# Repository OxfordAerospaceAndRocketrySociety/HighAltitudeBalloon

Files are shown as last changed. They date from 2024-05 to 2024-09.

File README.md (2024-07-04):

# HighAltitudeBalloon
A raspberry pi pico based GPS tracker and reciever for high altitude ballooning.

Please read [Setup.md](https://github.com/OxfordAerospaceAndRocketrySociety/HighAltitudeBalloon/blob/main/Setup.md) for instructions on installing the dependencies.

Please also have a look at [TODO.md](https://github.com/OxfordAerospaceAndRocketrySociety/HighAltitudeBalloon/blob/main/TODO.md) for infomation about what is yet to be done!

To build your own please see [Wiring.md](https://github.com/OxfordAerospaceAndRocketrySociety/HighAltitudeBalloon/blob/main/Wiring.md), it has a table of all of the connections nececary.

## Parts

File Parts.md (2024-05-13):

### GPS Module x1  - £23.99:
https://store.uputronics.com/index.php?route=product/product&path=60_64&product_id=72
### LORA Transciever x5 - £9.50:
https://store.uputronics.com/index.php?route=product/product&path=61&product_id=69
### Pi Pico (Reciever MCU) x3 - £4.42:
https://uk.rs-online.com/web/p/raspberry-pi/2122162?gb=s
### Pi SD Card x1 - £7.08:
https://uk.rs-online.com/web/p/sd-cards/1958347?gb=s
### Micro usb cable (5 pack) - £6.99:
https://www.amazon.co.uk/PEAKLIFT-Charging-Charger-Compatible-Motorola/dp/B098JMKVDL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
### AA Power Bank x1 - £5.99:
https://www.amazon.co.uk/Mercury-Emergency-USB-Power-Bank/dp/B0168K5FTQ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
### Lithium Batteries (4 pack) x1 - £7.99:
https://www.amazon.co.uk/Energizer-Ultimate-Lithium-Batteries-Pack/dp/B000IWW1G6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

We also need some single core wire for antennae, and connecting the components.

## Total: £103.96

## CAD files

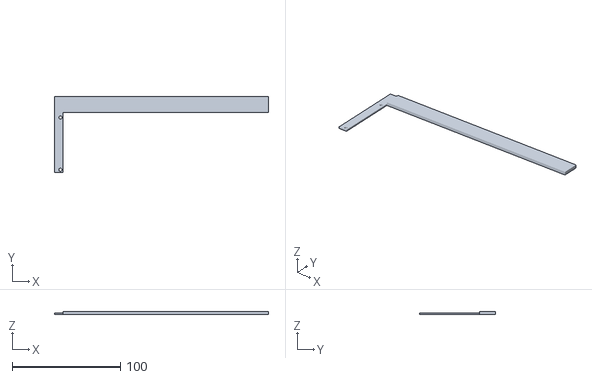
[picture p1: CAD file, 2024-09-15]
3D Printed Parts/RightSide.stl
198.0 x 70.3 x 3.00

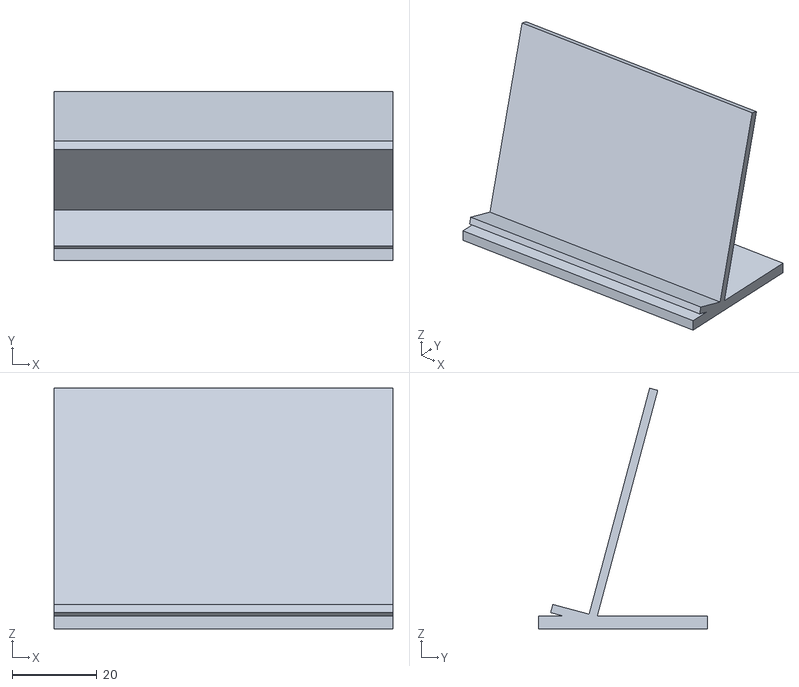
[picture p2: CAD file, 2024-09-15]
3D Printed Parts/Stand.stl
80.0 x 40.0 x 56.8

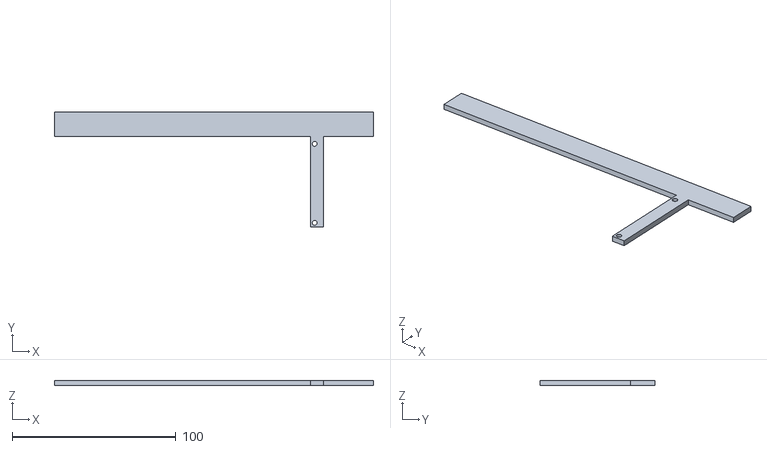
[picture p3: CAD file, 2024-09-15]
3D Printed Parts/LeftSide.stl
195.0 x 70.3 x 3.00

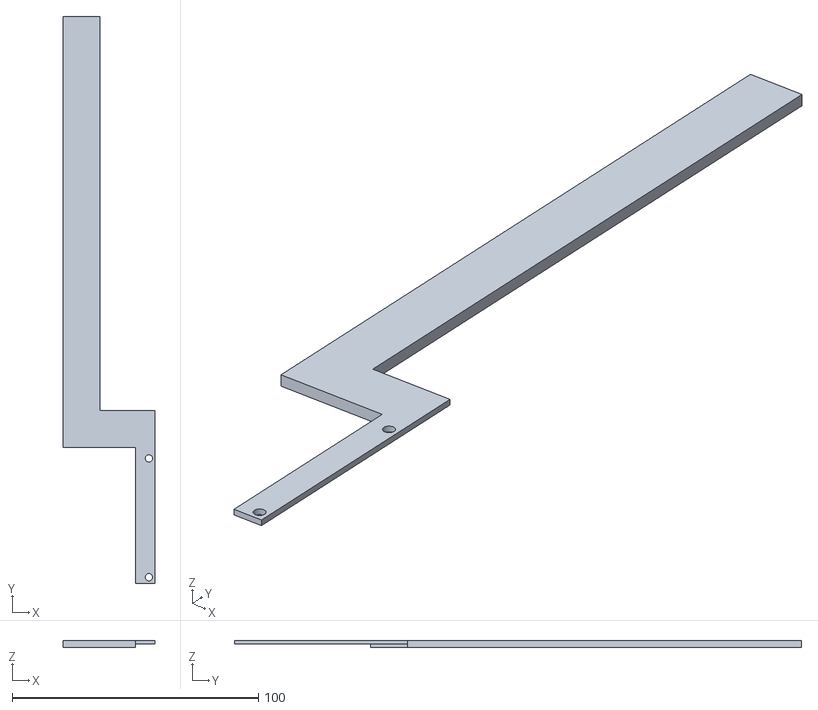
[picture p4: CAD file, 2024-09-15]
3D Printed Parts/TopSide.stl
37.5 x 230.3 x 3.00

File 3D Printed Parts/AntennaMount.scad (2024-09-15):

//2024 Oxford Aerospace and Rocketry Society
//Layout for the tracker / reciever PCB
//Comment out each individual part to print

$fn = 20; //20 Sides for each hole

difference(){
    union(){
        color("DodgerBlue",1) //PCB
        translate([0,0,3])
            cube([76.2,55.27,0.5]);
        
        translate([76.2-8,0,0])
            union(){
                color("ForestGreen", 1)
                    rightSide();
                color("FireBrick", 1)
                    topSide();
            }
        color("DarkSlateGray", 1)
            leftSide();
    }
        translate([2.54,2.54,0])//Mounting Holes
            cylinder(r = 1.5, h = 4);
        translate([2.54,50.8,0])
            cylinder(r = 1.5, h = 4);
        translate([73.66,50.8,0])
            cylinder(r = 1.5, h = 4);
        translate([73.66,2.54,0])
            cylinder(r = 1.5, h = 4);
}


module rightSide(){
    cube([8,55.27+15,1.5]);
    translate([8,55.27,0])
        cube([190,15,3]);
}

module topSide(){
    translate([0,0,1.5])
        cube([8,55.27+15,1.5]);
    translate([-22-7.5,55.27,0])
        cube([15,175,3]);
    translate([-22+7.5,55.27,0])
        cube([22-7.5,15,3]);
    
}

module leftSide(){
    cube([8,55.27,3]);
    translate([22-195+16.5,55.27,0])
        cube([195,15,3]);
    
}

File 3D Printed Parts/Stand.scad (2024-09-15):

//2024 Oxford Aerospace and Rocketry Society
//Simple stand for displaying a tracker

cube([80,40,3],center = true); //Base

translate([0,0,56/2]) //Back stand
rotate([75,0,0])
cube([80,56,2],center = true);

translate([0,-12,2]) //Front rest
rotate([-15,0,0])
cube([80,10,2],center = true);

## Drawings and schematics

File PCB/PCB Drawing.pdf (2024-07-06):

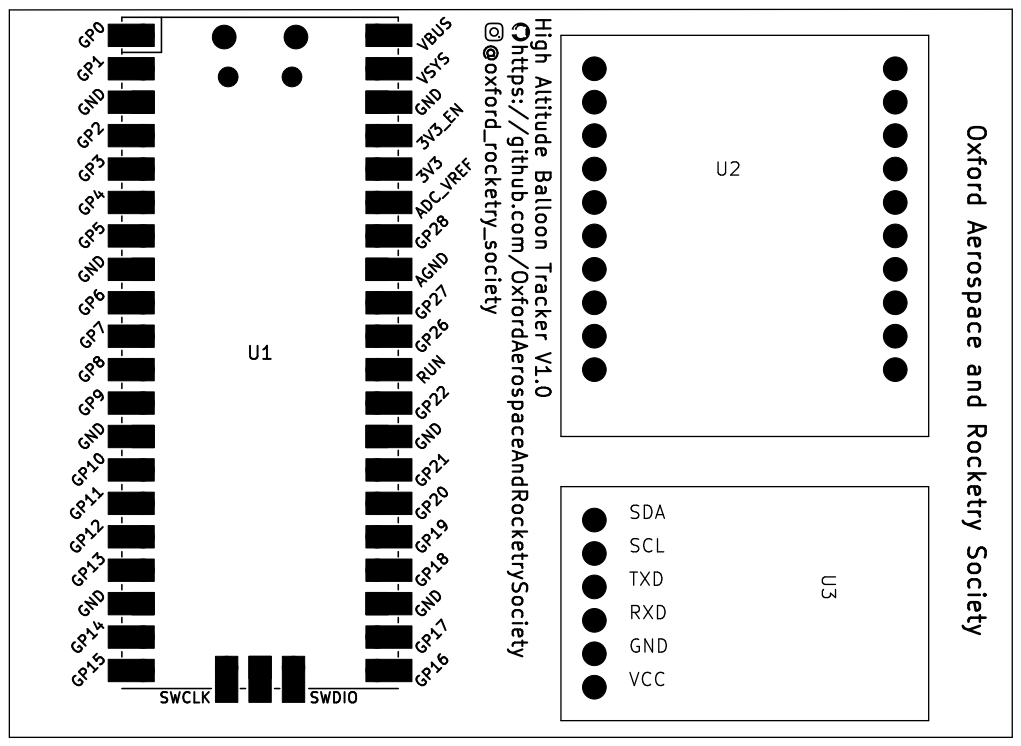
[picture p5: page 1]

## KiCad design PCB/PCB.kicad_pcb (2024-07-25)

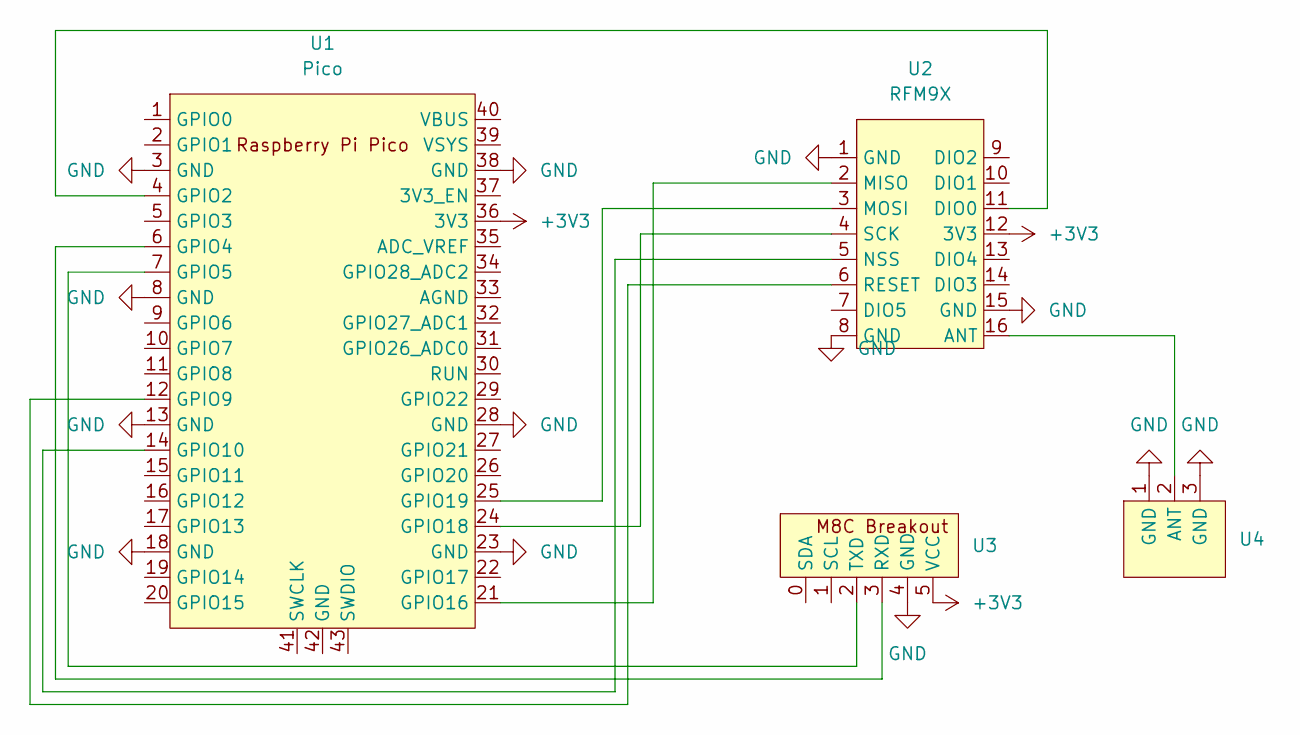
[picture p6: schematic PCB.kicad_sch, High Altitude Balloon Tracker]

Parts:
U1: Pico; RPi_Pico_SMD_TH
U2: RFM9X
U3: M8C Pico Breakout
U4: Antenna

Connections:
+3V3: U1.36 (3V3), U2.12 (3V3), U3.5 (VCC)
GND: U1.3 (GND), U1.8 (GND), U1.13 (GND), U1.18 (GND), U1.23 (GND), U1.28 (GND), U1.38 (GND), U2.1 (GND), U2.8 (GND), U2.15 (GND), U3.4 (GND), U4.1 (GND), U4.3 (GND)
unnamed: U1.4 (GPIO2), U2.11 (DIO0)
unnamed: U1.6 (GPIO4), U3.3 (RXD)
unnamed: U1.7 (GPIO5), U3.2 (TXD)
unnamed: U1.12 (GPIO9), U2.6 (RESET)
unnamed: U1.14 (GPIO10), U2.5 (NSS)
unnamed: U1.21 (GPIO16), U2.2 (MISO)
unnamed: U1.24 (GPIO18), U2.4 (SCK)
unnamed: U1.25 (GPIO19), U2.3 (MOSI)
unnamed: U2.16 (ANT), U4.2 (ANT)

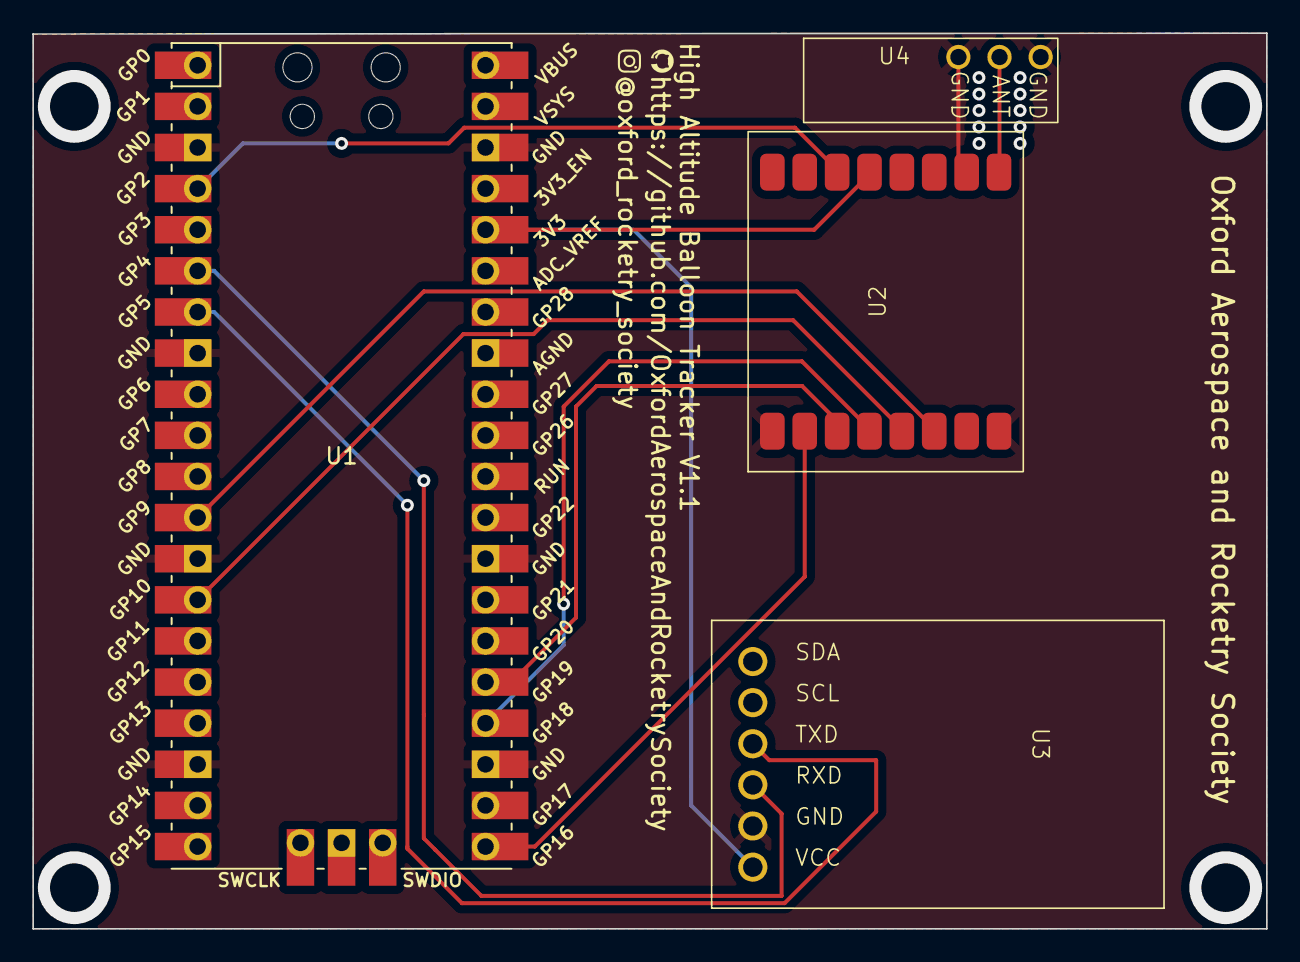
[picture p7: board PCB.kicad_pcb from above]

Board: 2 copper layers, 76.2 x 55.3 mm, 4 parts (0 on the bottom side), 11 nets.

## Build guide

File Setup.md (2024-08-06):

# Setup
## Arduino Setup
1. Install the [arduino ide](https://www.arduino.cc/en/software), latest version (something like 2.3.x). Make sure you install any drivers when prompeted.
2. Open the board manager using (the circuit board icon).
3. Search for and install Arduino Mbed OS RP2040 Boards.
4. Download the [TinyGPS++](https://github.com/mikalhart/TinyGPSPlus/archive/master.zip) Library.
5. Open Sketch -> Include Library -> Add .ZIP Library and select the zip file you just downloaded.
6. Open the library manager ```Ctrl+Shift+I``` and install ```LoRa by Sandeep Mistry```.
7. Install ```CRC by Rob Tillaart``` in the library manager.
8. You're done!
## Python Dependencies
Please use pip to install `pyserial`, `crc`, `sondehub`and `tkintermapview`.
## KiCad Libraries
Pi Pico - https://github.com/ncarandini/KiCad-RP-Pico

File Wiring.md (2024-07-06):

# Pi Pico Wiring
Please see https://pico.pinout.xyz/ for the physical location of pins.
## RFM 96

| RFM 96 | Pi Pico |
| ---| ---|
|VCC | 3V3 Out|
|GND | Ground|
|SCK | SCK (GP 18)|
|MISO | MISO (GP 16)|
|MOSI |	MOSI (GP 19)|
|NSS | GP 10|
|NRESET| GP 9|
|DIO0| GP 2|

## GPS Module
| GPS | Pi Pico |
| ---| ---|
|VCC | 3V3 Out|
|GND | Ground|
|TX | GP 5 |
|RX| GP 4|

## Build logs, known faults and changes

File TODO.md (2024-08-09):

# Avionics TODO List
## Tracker
* Add velocity to message?
## Desktop Program
## Logger
* Write code for taking pictures on the pi zeros.
* Write code for saving the data from the muon detector.

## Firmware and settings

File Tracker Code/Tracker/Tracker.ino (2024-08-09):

//Oxford Aerospace and Rocketry 2024
#include <SPI.h>
#include <LoRa.h>
#include <TinyGPSPlus.h>
#include "CRC16.h"
#include "CRC.h"

//Define device details
String FlightName = "OXHABTEST1";
String DEVICE = "Pico Tracker";
String VERSION = "V1.0";

// The TinyGPSPlus and Checksum objects
TinyGPSPlus gps;
CRC16 crc;

//Define the GPS Pins
UART GPSserial(4, 5, NC, NC);

//LoRa Transmission freqeuncy (hz) 
int freq = 434.145E6; 

//Setup message counters
int count = 0;
int pkt_count = 0;

//Setup the clock
String hms;

//Setup the altitude
String altitude;

void setup() {
  //Setup the serial connection
  Serial.begin(57600);
  Serial.println("");
  Serial.print(DEVICE);
  Serial.print("");
  Serial.println(VERSION);
  Serial.println("");

  //Setup the builtin LED
  pinMode(LED_BUILTIN, OUTPUT);

  //Initialise the GPS connection
  GPSserial.begin(9600);

  if (!LoRa.begin(freq)) {
    Serial.println("Starting LoRa failed!");
    //Flash error code
    digitalWrite(LED_BUILTIN, HIGH);
    delay(500);
    digitalWrite(LED_BUILTIN, LOW);
    while (1);
  }
  //Limit power to the UK regulation 10 mW
  LoRa.setTxPower(10);
}

void loop() {
  while (GPSserial.available() > 0) {
    //Pass the raw GPS data to the tiny GPS library
    gps.encode(GPSserial.read());
    //Send a new message every time the GPS time updates
    if (gps.time.isUpdated()) {
      sendInfo();
    }
  }
}

void sendInfo() {
  //Create a UKHAS Standard message (using: https://www.daveakerman.com/?p=2987)
  String message;
  formatTime(gps.time.hour(), gps.time.minute(), gps.time.second());
  formatAltitude(gps.altitude.meters());

  message = FlightName+","+String(count)+","+hms+","+String(gps.location.lat(),6)+","+String(gps.location.lng(),6)+","+String(altitude);

  Serial.print("Sending packet: ");
  Serial.println(pkt_count);

  if (gps.location.lat() != 0.0) {
    digitalWrite(LED_BUILTIN, LOW);
    LoRa.beginPacket();
    LoRa.print("$$");
    LoRa.print(message);

    //Append the CRC16 Checksum to the end of the message
    LoRa.print("*");
    //CRC16 Configuration - Polynome: 0x1021, Initial Value: 0xFFFF, Final Value: 0x0000
    LoRa.print(calcCRC16((uint8_t *)message.c_str(),message.length(),4129,65535,0), HEX);
    LoRa.endPacket();
    count++;
  }
  else {
    digitalWrite(LED_BUILTIN, HIGH);
    LoRa.beginPacket();
    LoRa.print("??");
    LoRa.print(FlightName);
    LoRa.print(" NO GPS FIX - TIME: ");
    LoRa.print(hms);
    LoRa.endPacket();
  }
  pkt_count++;
}

void formatTime(int h, int m, int s) {
  //Setup Arrays for Storing Time Strings
  String H;
  String M;
  String S;

  //Add leading zero
  if (h < 10) {
    H = "0" + String(h);
  } else {
    H = String(h);
  }
  if (m < 10) {
    M = "0" + String(m);
  } else {
    M = String(m);
  }
  if (s < 10) {
    S = "0" + String(s);
  } else {
    S = String(s);
  }

  //Format the time
  hms = H+":"+M+":"+S;
}

void formatAltitude(float alt) {
  int length = String(int(round(alt))).length();
  if (length > 5) {
    //Set maxiumum altitude
    altitude = "99999";
  } else {
    altitude = String(int(round(alt)));
  }
}

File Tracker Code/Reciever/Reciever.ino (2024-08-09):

//Derived from the examples located at:
//https://github.com/sandeepmistry/arduino-LoRa/tree/master?tab=readme-ov-file
#include <SPI.h>
#include <LoRa.h>

void setup() {
  Serial.begin(9600);
  while (!Serial);

  Serial.println("LoRa Receiver");

  if (!LoRa.begin(434.145E6)) {
    Serial.println("Starting LoRa failed!");
    while (1);
  }
}

void loop() {
  // try to parse packet
  int packetSize = LoRa.parsePacket();
  if (packetSize) {
    // received a packet
    Serial.print("Message=");

    // read packet
    while (LoRa.available()) {
      Serial.print((char)LoRa.read());
    }

    // print RSSI of packet
    Serial.println("");
    Serial.print("RSSI:");
    Serial.println(LoRa.packetRssi());
  }
}

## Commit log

2024-06-11 Added files for GPS tests
    Arduino programs for testing the UBLOX GPS module on the raspberry pi pico
2024-06-11 Added setup code for GPS (not working)
    [GPSTest0.ino, GPSTest1.ino]
2024-07-04 Test out LoRa Modules
    Also added some additional documentation for wiring the pico
2024-07-06 Added a V1 of the tracker PCB
    [PCB.kicad_pcb, PCB.kicad_sch]
2024-07-07 Added gerber files for PCB
    [PCB-B_Cu.gbl, PCB-B_Mask.gbs, PCB-B_Paste.gbp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]
2024-07-22 Added LED Error Codes
    [GPSTest2.ino, Tracker.ino]
2024-07-25 Added time to no fix message
    [GPSTest0.ino, Tracker.ino]
2024-07-25 Updated PCB to use SMT RFM9X
    PCB now on v1.1, currently untested
    [PCB-B_Cu.gbl, PCB-B_Mask.gbs, PCB-B_Paste.gbp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]
2024-07-31 Updated code for correct checksum
    [GPSsimulator.ino, Tracker.ino, serialRead.py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]
2024-08-07 Quick fix for corrupted CRCs
    [serialRead.py, serialReadGUI.py]
2024-09-15 Added antenna mount CAD
    [AntennaMount.scad, LeftSide.stl, RightSide.stl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]
2024-09-26 Create LaptoplessTest0
    Folder for Receiver and Transmitter code, modified to be tested without a laptop (Because my laptop battery doesnt work)
